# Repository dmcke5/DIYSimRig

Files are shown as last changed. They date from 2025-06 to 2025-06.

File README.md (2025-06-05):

# CNCDan - DIY Sim Rig

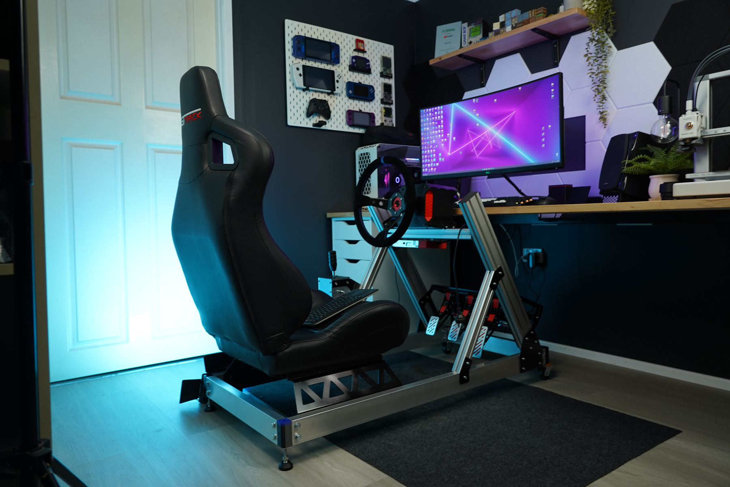
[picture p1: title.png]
DIY Sim Rig


This project is part of my DIY Sim racing series. This sim rig is designed to work with all of my DIY sim racing accessories along with any seat with rail hole spacing of 357x300mm (Width x Length).

The seat I used is from a Next Level Racing GTRacer 2.0. If you find a seat that is compatible with this design without any modifications, let me know and I will include a list of compatible models!

Be cautious with the steering bar brackets. The cut file is the same for both sides but you will need to countersink the holes on opposite sides so you have a mirrored pair of plates. I have uploaded a .STEP file for both so you can see what I mean.

If you decide to make the flat brackets yourself by hand, you should be able to open the DXF files and print them at 1:1 scale onto paper to use as a template. You could also 3D print the .STEP files and use them as a template.

Here's the wiring diagram to connect the Pedals to the FFBeast Wheel:
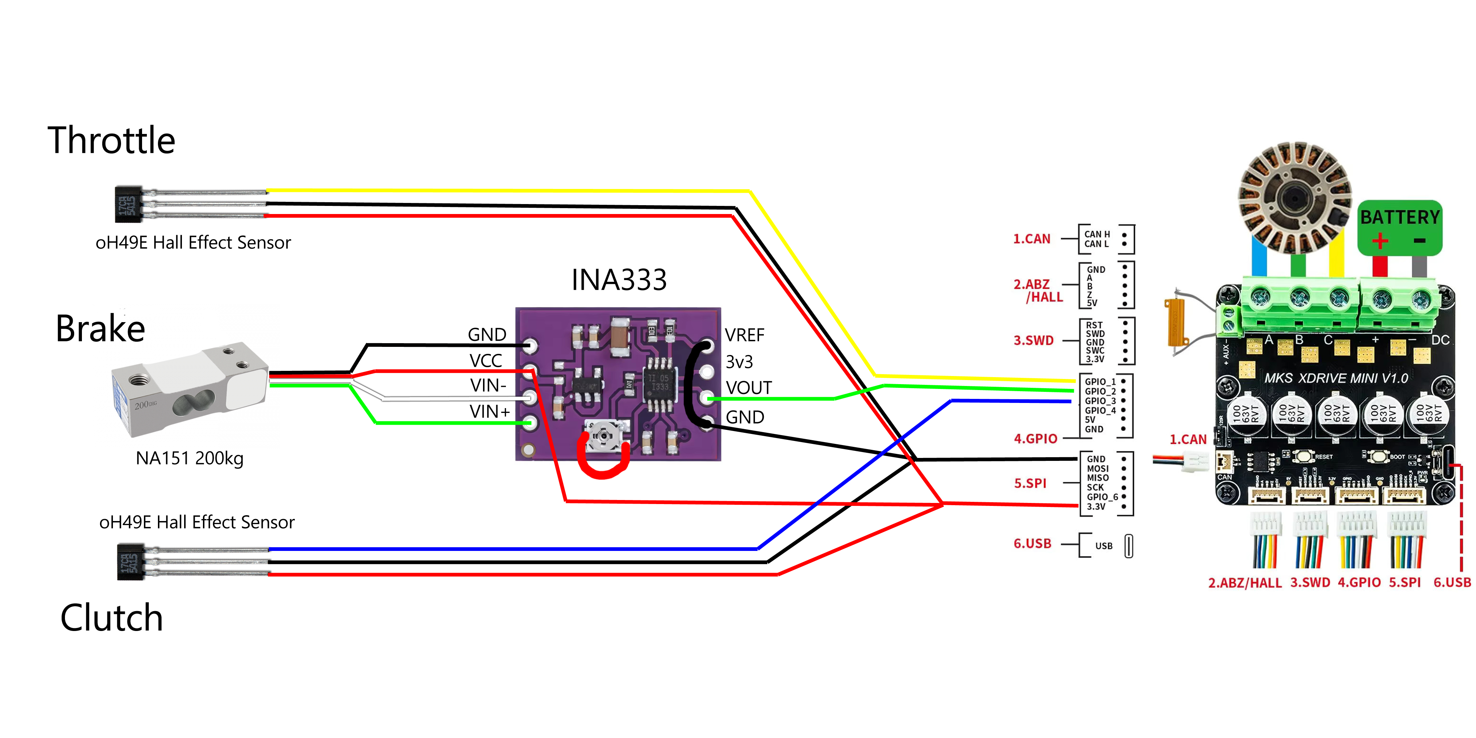
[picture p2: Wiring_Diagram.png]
Wiring Diagram

The order of the GPIO connections doesn't matter, just map the pedals as the correct inputs in the game and you'll be set!

If you want to build the whole set, here are the links to the other projects featured in this video!

Shifter: https://github.com/dmcke5/H-Shifter

Pedals: https://github.com/dmcke5/SimPedals

Wheel: https://github.com/dmcke5/FFBeast-Wheel

Finally, here's a link to the INA333 board I used to get the load cell working with the FFBeast wheel: https://www.aliexpress.com/item/1005007130064459.html

Link to video: https://youtu.be/oFvz3rBkJsg

#### Bill of Materials

2m of 8040 Extrusion

1m of 4040 Extrusion

3.5m of 70x30x3 Aluminium RHS

#### Nuts, Bolts and Washers

34x M5 4040 T-Nuts

50x M5x16 SHCS

50x M5 Washers

16x M8x40 Hex Head Bolts

4x M8x20 Hex Head Bolts

24x M8 Nyloc Nuts

36x M8 Washers

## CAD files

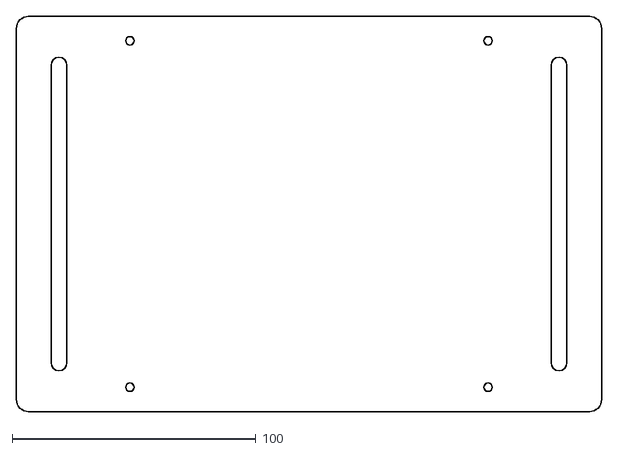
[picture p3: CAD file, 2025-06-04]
Laser Cut Parts/3mm Steering Wheel Mount x1.DXF
240.0 x 162.0

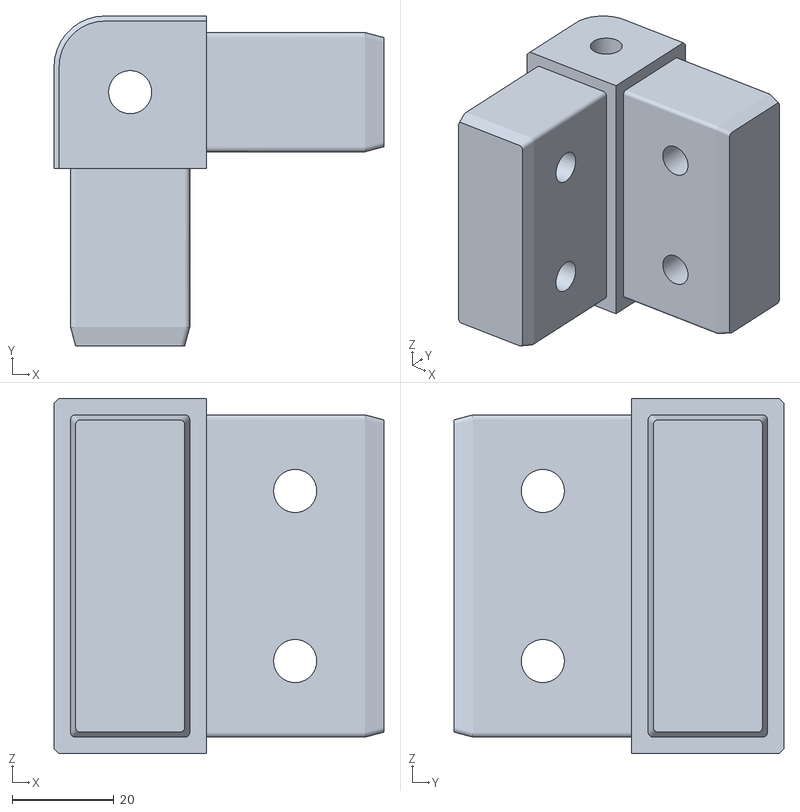
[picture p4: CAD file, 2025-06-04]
Printed Parts/PETG Corner Bracket.STL
65.0 x 65.0 x 70.0

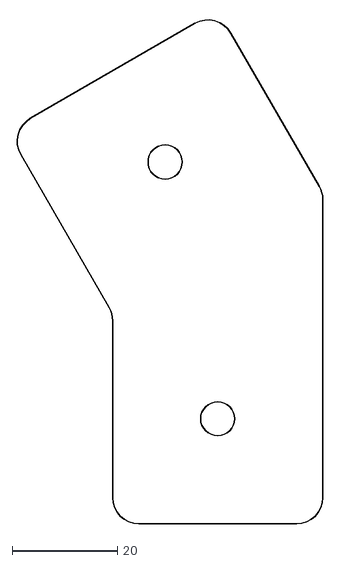
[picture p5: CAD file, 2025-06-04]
Laser Cut Parts/3mm Brace Brackets x4.DXF
58.3 x 96.6

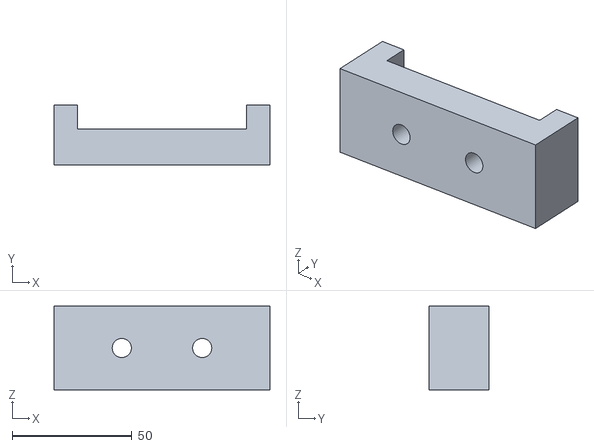
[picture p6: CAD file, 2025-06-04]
Printed Parts/Chassis Corner Drill Jig.STL
90.0 x 25.0 x 35.0

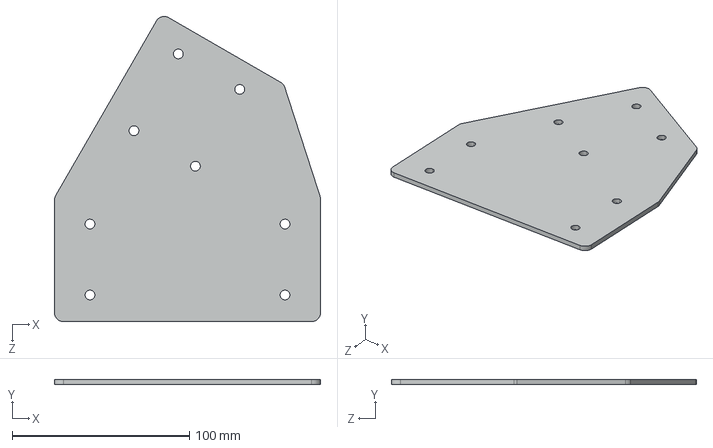
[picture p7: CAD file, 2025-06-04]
Laser Cut Parts/Steering Upright Brackets.STEP
150.0 x 3.00 x 172.1 mm

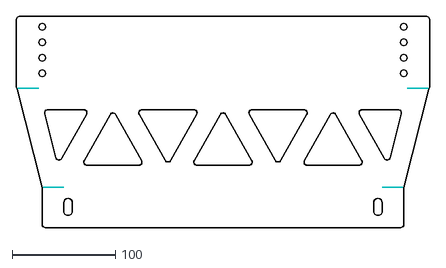
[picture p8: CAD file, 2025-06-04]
Laser Cut Parts/3mm Seat Bracket x2.DXF
400.0 x 204.3

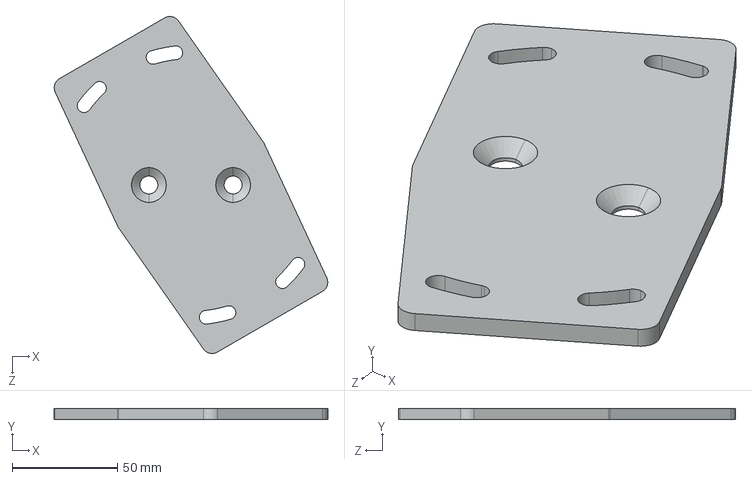
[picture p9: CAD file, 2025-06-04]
Laser Cut Parts/Steering Bar Bracket Right.STEP
130.0 x 5.00 x 160.1 mm

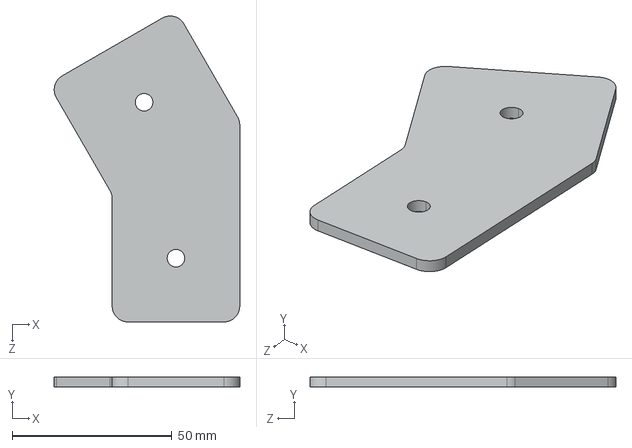
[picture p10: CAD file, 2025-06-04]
Laser Cut Parts/Brace Brackets.STEP
58.2 x 3.00 x 95.9 mm

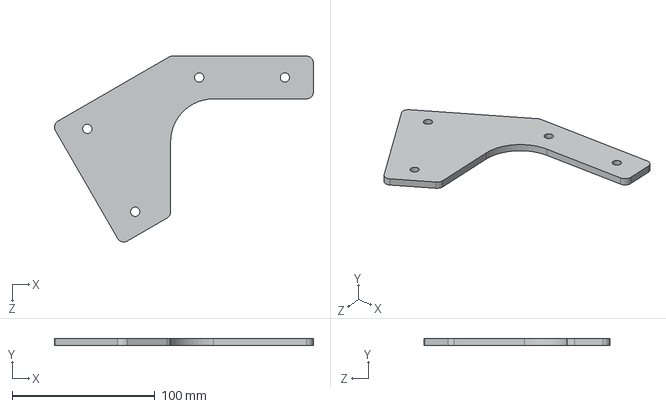
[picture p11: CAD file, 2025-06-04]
Laser Cut Parts/Shifter Bracket.STEP
181.3 x 5.00 x 130.2 mm

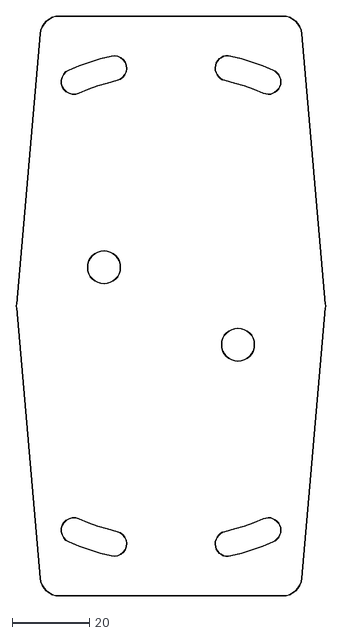
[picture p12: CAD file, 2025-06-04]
Laser Cut Parts/5mm Steering Bar Bracket x2.DXF
80.0 x 150.0

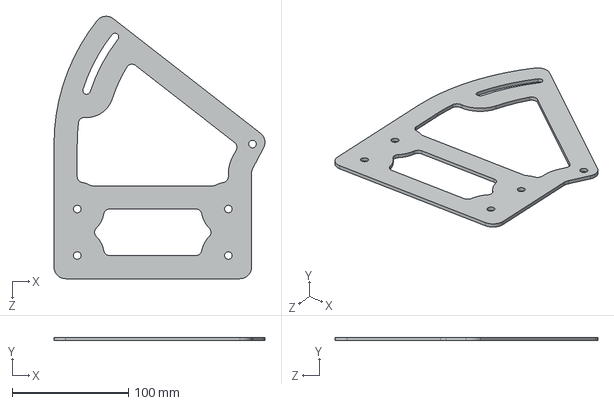
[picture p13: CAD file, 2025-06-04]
Laser Cut Parts/Pedal Mounting Bracket.STEP
181.5 x 3.00 x 225.9 mm

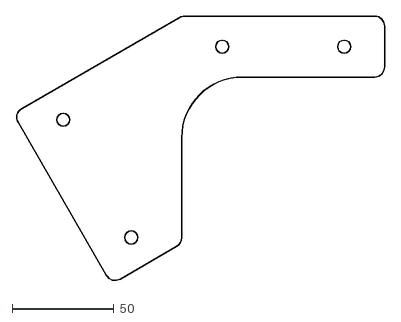
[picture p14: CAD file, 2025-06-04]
Laser Cut Parts/3mm Shifter Bracket x1.DXF
181.5 x 130.9

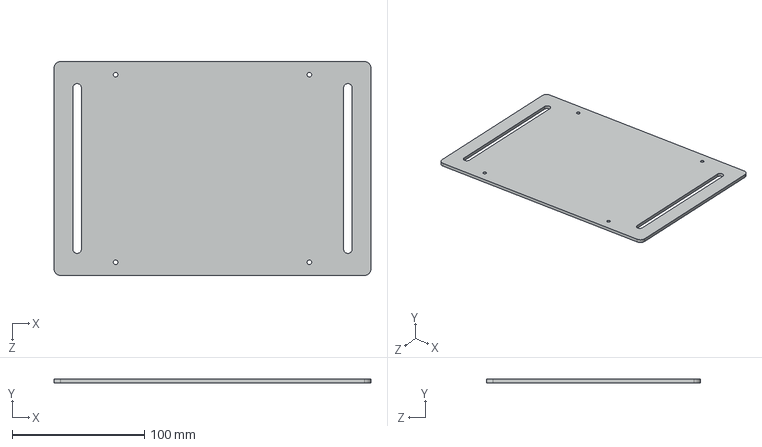
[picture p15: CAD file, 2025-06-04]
Laser Cut Parts/Steering Wheel Mount.STEP
240.0 x 3.00 x 162.0 mm

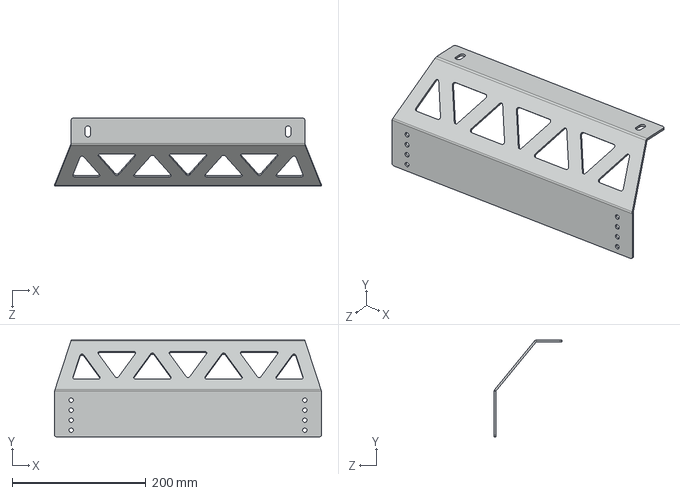
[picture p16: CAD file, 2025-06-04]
Laser Cut Parts/Seat Bracket.STEP
400.0 x 145.0 x 101.5 mm

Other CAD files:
Laser Cut Parts/Steering Bar Bracket Left.STEP
Laser Cut Parts/3mm Steering Upright Brackets x2.DXF
Laser Cut Parts/3mm Pedal Mounting Bracket x2.DXF

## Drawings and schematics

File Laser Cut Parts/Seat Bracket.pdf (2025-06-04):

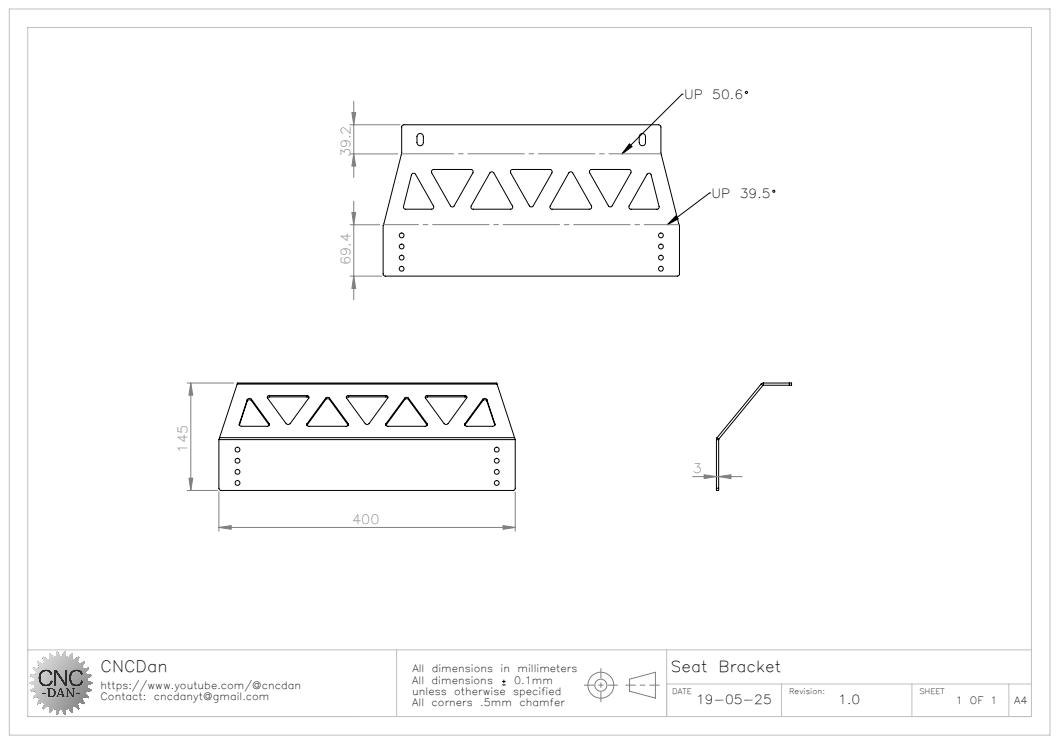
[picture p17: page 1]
All dimensions

CNCDan https://www.youtube.com/@cncdan Contact: cncdanyt@gmail.com | | Seat Bracket

All dimensions in millimeters
unless otherwise specified
All corners .5mm chamfer

DATE 19-05-25 | Revision: 1.0 | SHEET 1 OF 1 | A4

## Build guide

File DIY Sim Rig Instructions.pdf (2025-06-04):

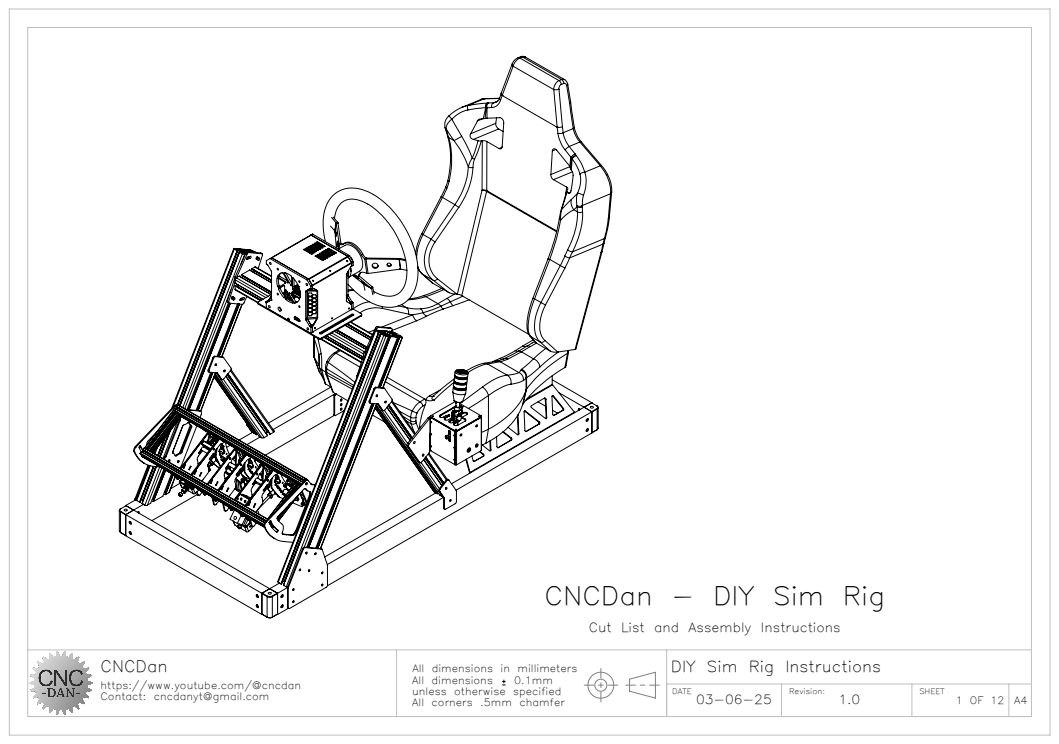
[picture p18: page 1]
All dimensions

CNCDan - DIY Sim Rig

Cut List and Assembly Instructions

CNCDan https://www.youtube.com/@cncdan Contact: cncdanyt@gmail.com | | DIY Sim Rig Instructions

All dimensions in millimeters
unless otherwise specified
All corners .5mm chamfer

DATE 03-06-25 | Revision: 1.0 | SHEET 1 OF 12 | A4

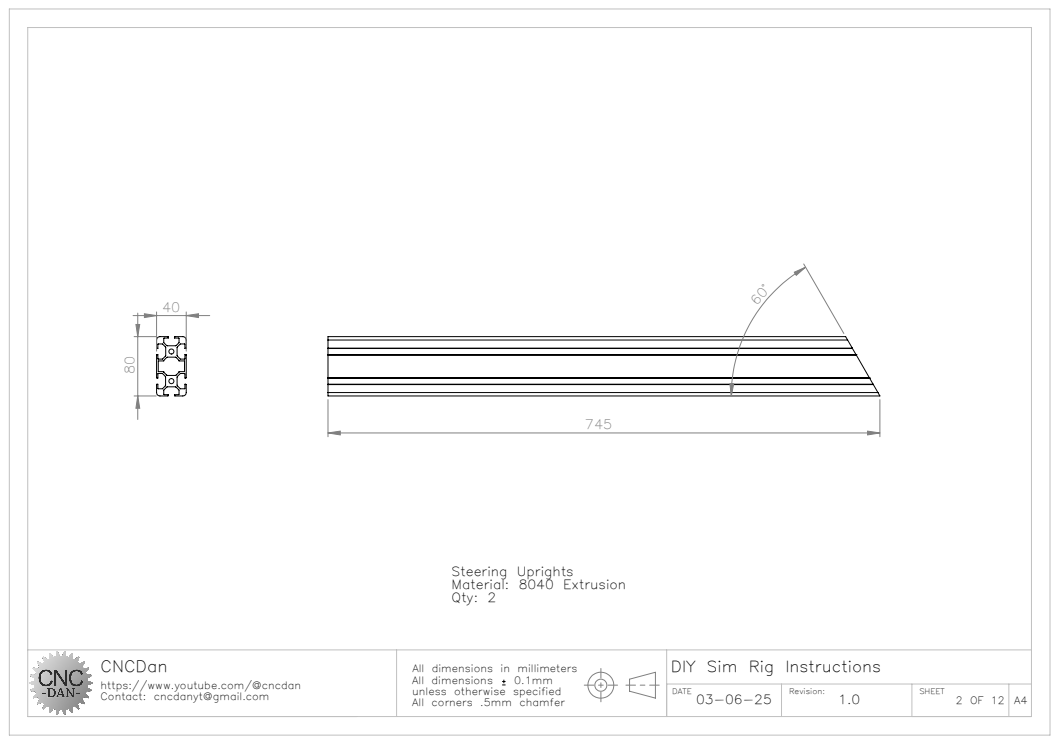
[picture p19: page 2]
Steering Uprights Material: 8040 Extrusion Qty: 2; All dimensions

CNCDan https://www.youtube.com/@cncdan Contact: cncdanyt@gmail.com | | DIY Sim Rig Instructions

All dimensions in millimeters
unless otherwise specified

DATE | Revision: | SHEET

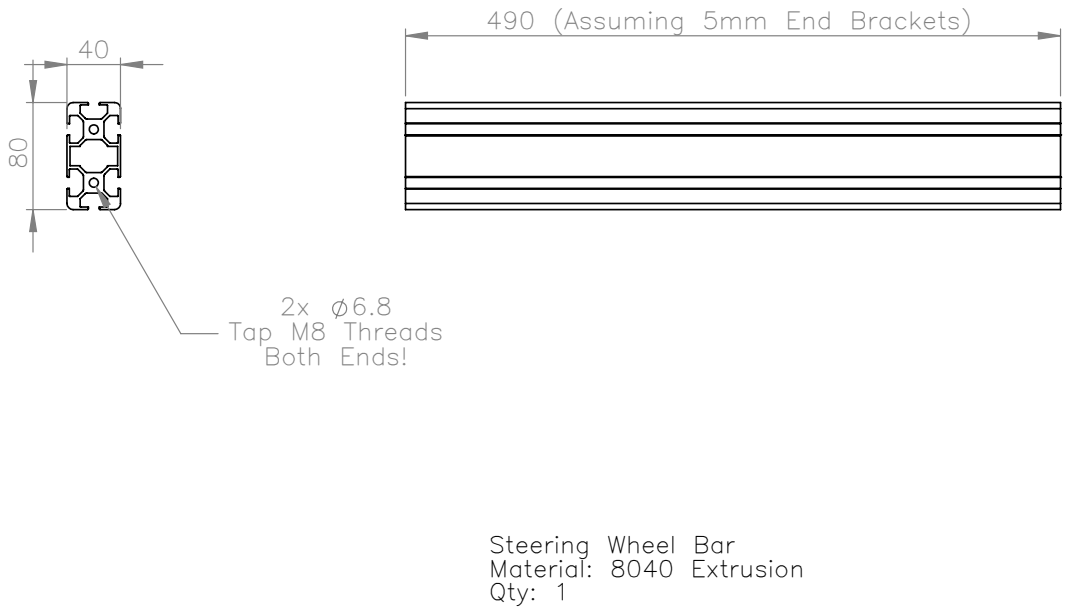
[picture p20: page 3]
Tap M8 Threads Both Ends!; All dimensions

490 (Assuming 5mm End Brackets)

Steering Wheel Bar
Material: 8040 Extrusion
Qty: 1

CNCDan https://www.youtube.com/@cncdan Contact: cncdanyt@gmail.com | | DIY Sim Rig Instructions

All dimensions in millimeters
unless otherwise specified

DATE | Revision: | SHEET

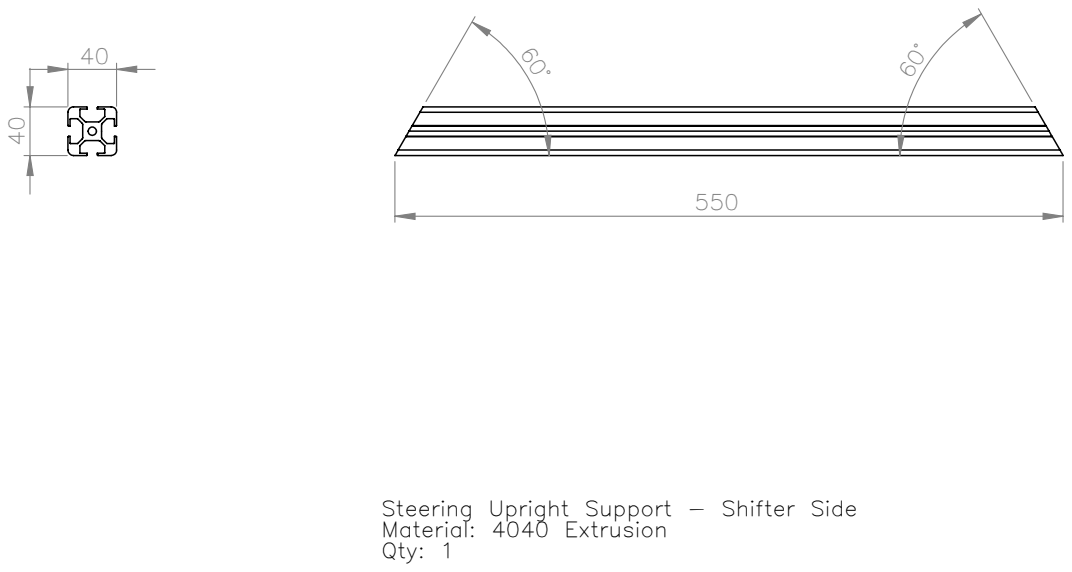
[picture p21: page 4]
All dimensions

Steering Upright Support - Shifter Side
Material: 4040 Extrusion
Qty: 1

CNCDan https://www.youtube.com/@cncdan Contact: cncdanyt@gmail.com | | DIY Sim Rig Instructions

All dimensions in millimeters
unless otherwise specified

DATE | Revision: | SHEET

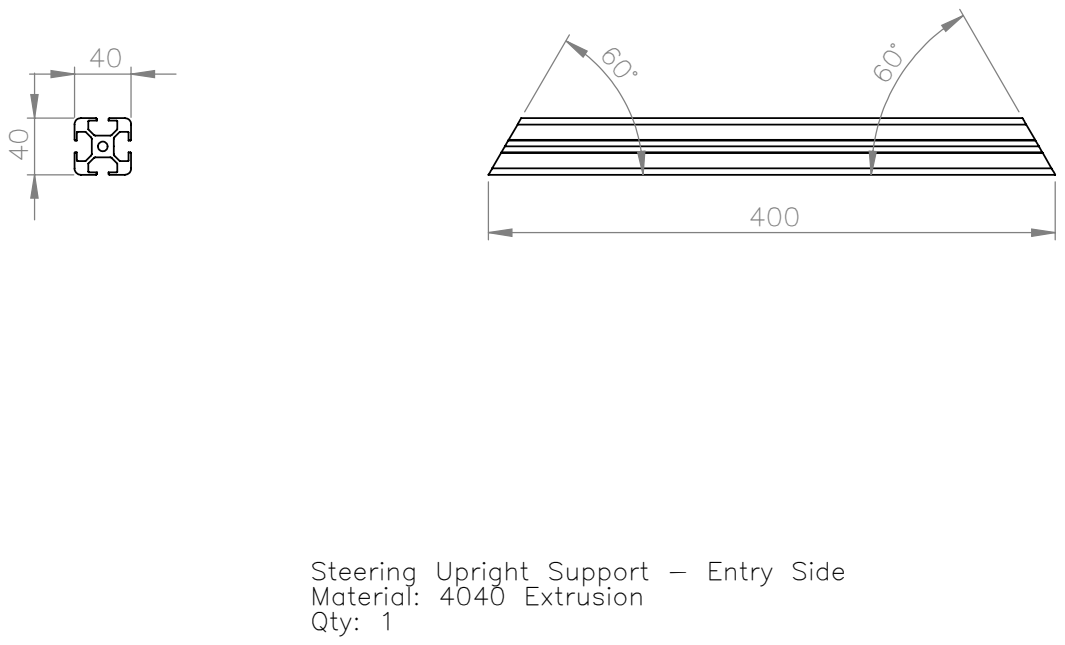
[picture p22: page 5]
All dimensions

Steering Upright Support - Entry Side
Material: 4040 Extrusion
Qty: 1

CNCDan https://www.youtube.com/@cncdan Contact: cncdanyt@gmail.com | | DIY Sim Rig Instructions

All dimensions in millimeters
unless otherwise specified

DATE | Revision: | SHEET

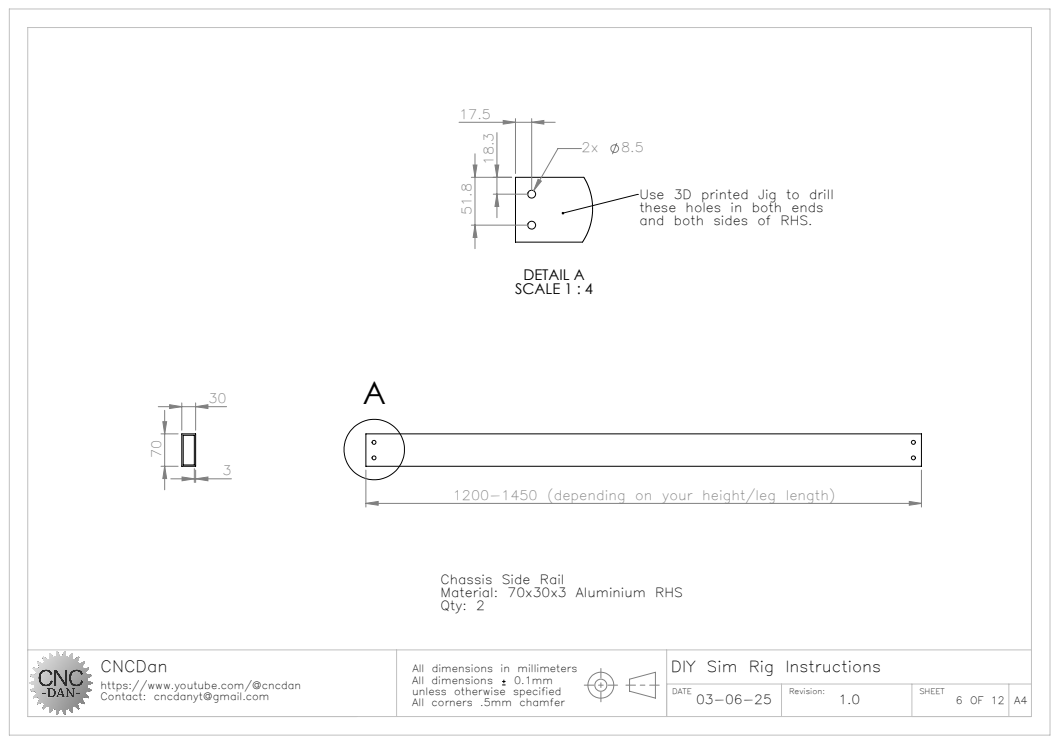
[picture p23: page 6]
DETAIL A SCALE 1 : 4; All dimensions

Use 3D printed Jig to drill
these holes in both ends
and both sides of RHS.

1200-1450 (depending on your height/leg length)

Chassis Side Rail
Material: 70x30x3 Aluminium RHS
Qty: 2

CNCDan https://www.youtube.com/@cncdan Contact: cncdanyt@gmail.com | | DIY Sim Rig Instructions

All dimensions in millimeters
unless otherwise specified

DATE | Revision: | SHEET

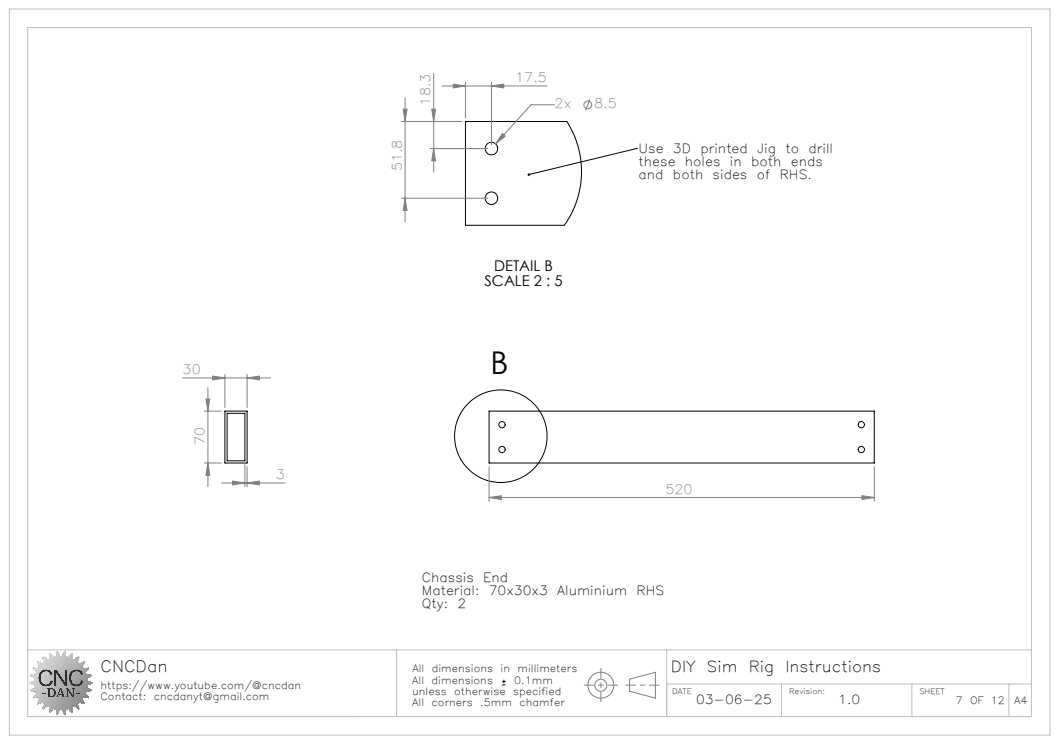
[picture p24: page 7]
DETAIL B SCALE 2 : 5; All dimensions

Use 3D printed Jig to drill
these holes in both ends
and both sides of RHS.

Chassis End
Material: 70x30x3 Aluminium RHS
Qty: 2

CNCDan https://www.youtube.com/@cncdan Contact: cncdanyt@gmail.com | | DIY Sim Rig Instructions

All dimensions in millimeters
unless otherwise specified

DATE | Revision: | SHEET

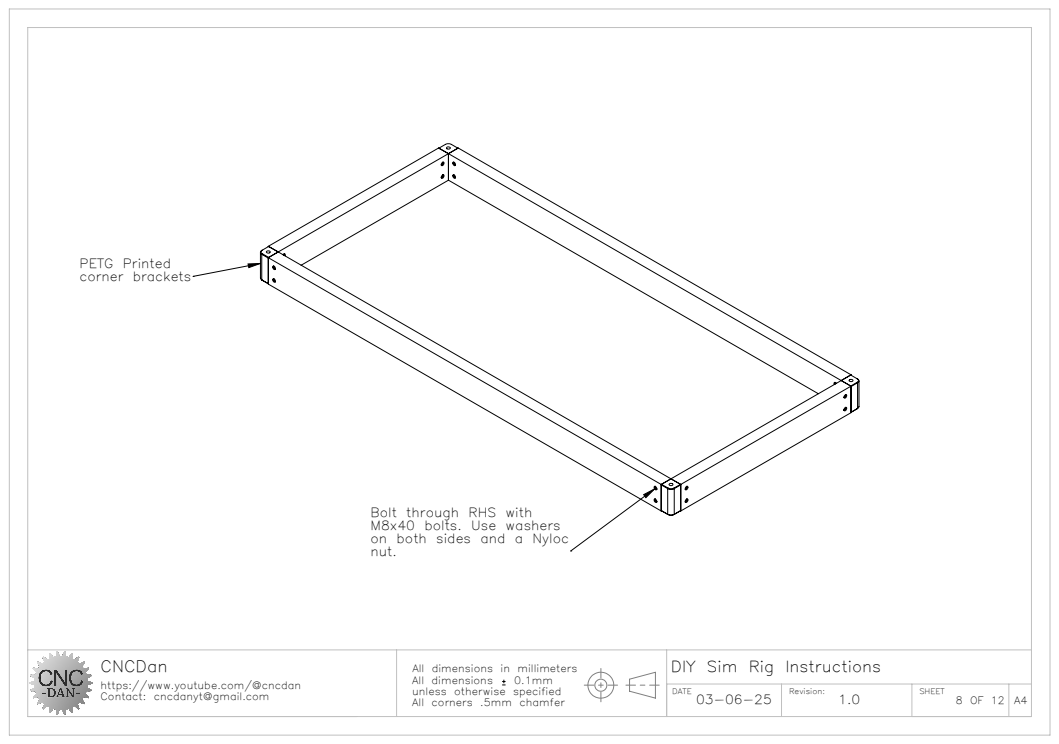
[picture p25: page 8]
PETG Printed corner brackets; All dimensions

Bolt through RHS with
M8x40 bolts. Use washers
on both sides and a Nyloc
nut.

CNCDan https://www.youtube.com/@cncdan Contact: cncdanyt@gmail.com | | DIY Sim Rig Instructions

All dimensions in millimeters
unless otherwise specified

DATE | Revision: 1.0 | SHEET 8 OF 12

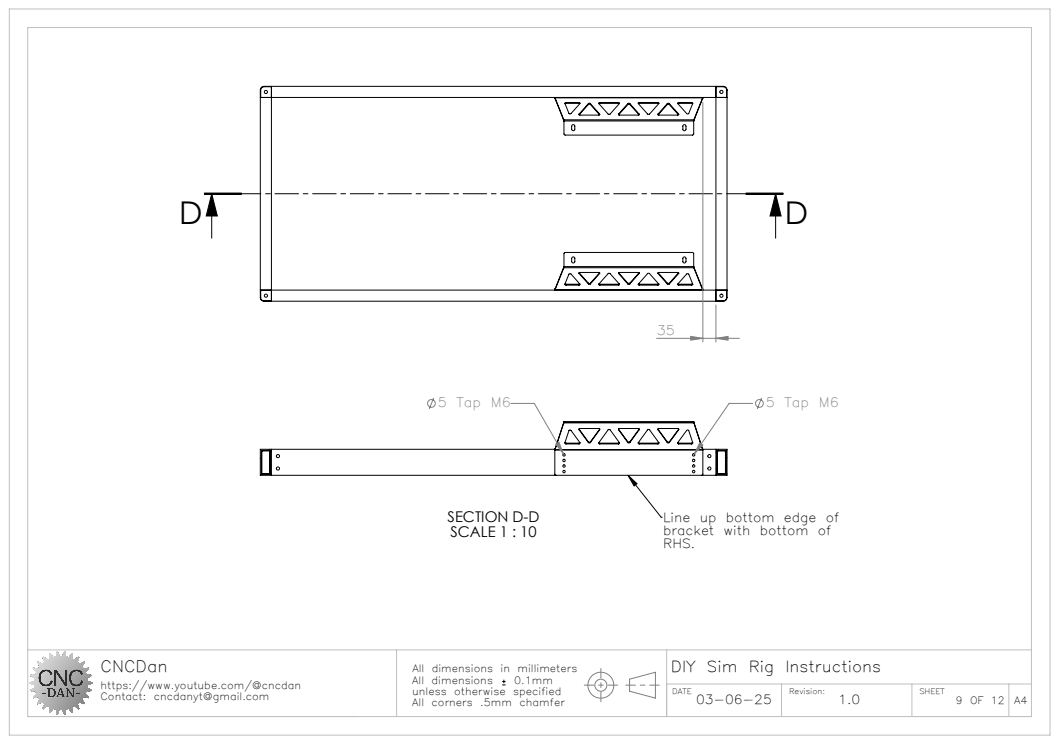
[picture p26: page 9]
5 Tap M6; SECTION D-D SCALE 1 : 10; All dimensions

Line up bottom edge of
bracket with bottom of
RHS.

CNCDan https://www.youtube.com/@cncdan Contact: cncdanyt@gmail.com | | DIY Sim Rig Instructions

All dimensions in millimeters
unless otherwise specified

DATE | Revision: 1.0 | SHEET 9 OF 12

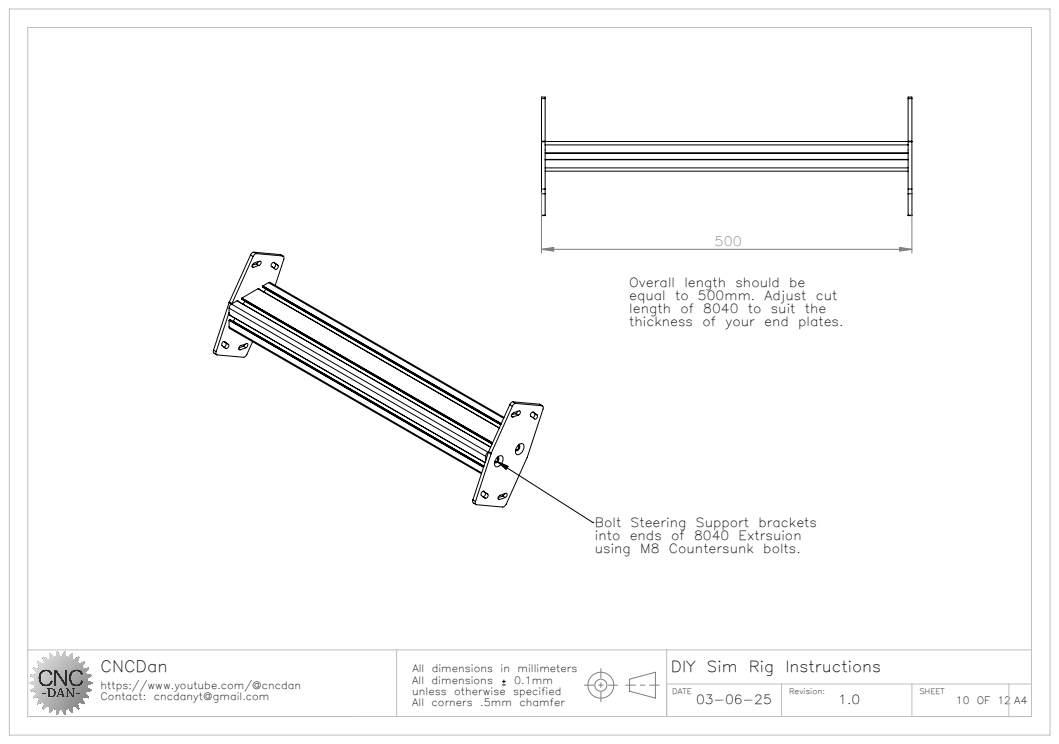
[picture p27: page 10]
All dimensions

Overall length should be
equal to 500mm. Adjust cut
length of 8040 to suit the
thickness of your end plates.

Bolt Steering Support brackets
into ends of 8040 Extrsuion
using M8 Countersunk bolts.

CNCDan https://www.youtube.com/@cncdan Contact: cncdanyt@gmail.com | | DIY Sim Rig Instructions

All dimensions in millimeters
unless otherwise specified

DATE | Revision: | SHEET

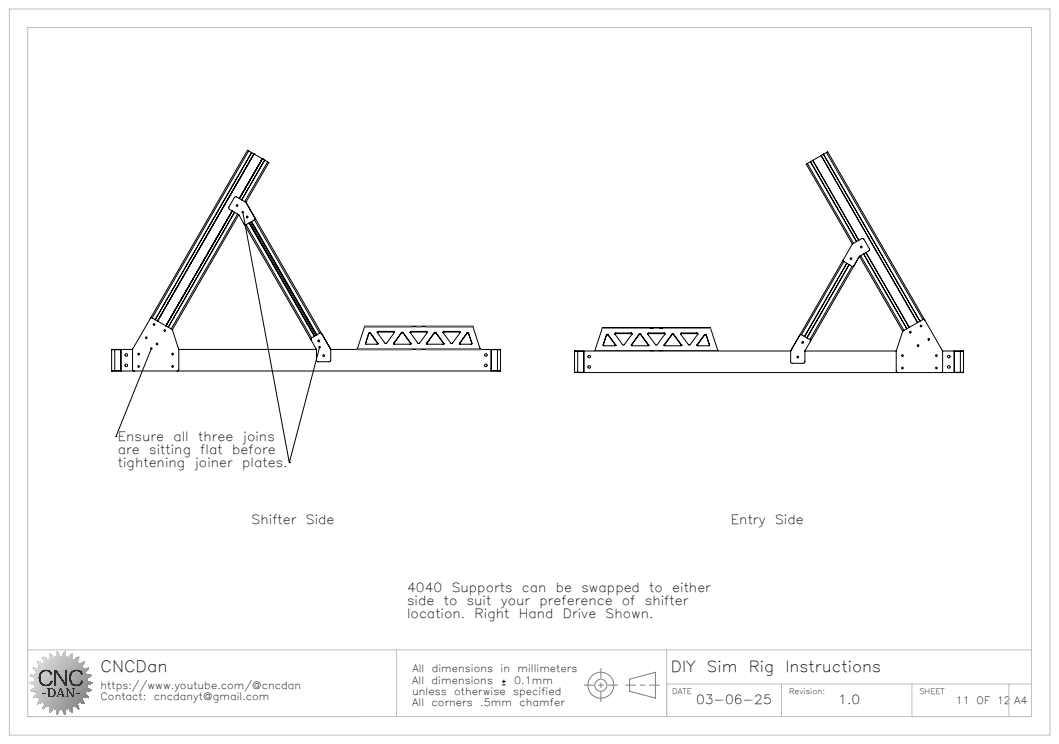
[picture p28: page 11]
Shifter Side; Entry Side; All dimensions

Ensure all three joins
are sitting flat before
tightening joiner plates.

4040 Supports can be swapped to either
side to suit your preference of shifter
location. Right Hand Drive Shown.

CNCDan https://www.youtube.com/@cncdan Contact: cncdanyt@gmail.com | | DIY Sim Rig Instructions

All dimensions in millimeters
unless otherwise specified

DATE | Revision: | SHEET

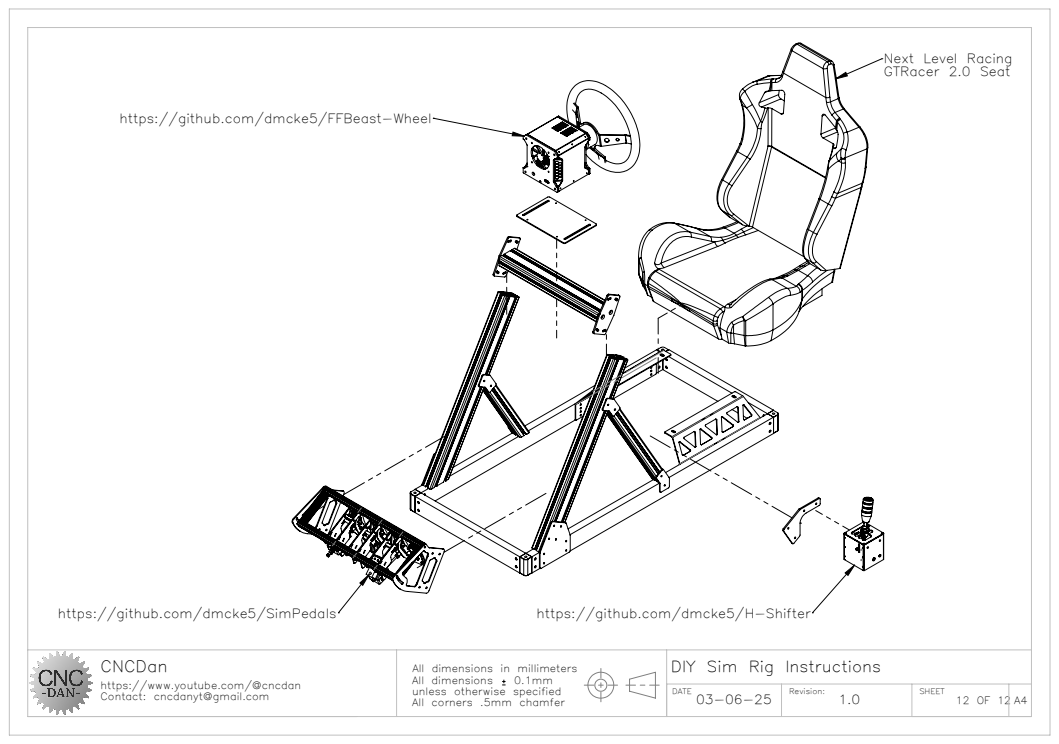
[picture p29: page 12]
All dimensions

Next Level Racing
GTRacer 2.0 Seat

https://github.com/dmcke5/FFBeast-Wheel

CNCDan https://www.youtube.com/@cncdan Contact: cncdanyt@gmail.com | | DIY Sim Rig Instructions

All dimensions in millimeters
unless otherwise specified

DATE | Revision: 1.0 | SHEET 12 OF 12

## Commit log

2025-06-04 Add cut files and update readme
    [3mm Brace Brackets x4.DXF, 3mm Pedal Mounting Bracket x2.DXF, 3mm Seat Bracket x2.DXF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]
2025-06-04 Update readme to include wiring diagram
2025-06-04 Updated BOM
